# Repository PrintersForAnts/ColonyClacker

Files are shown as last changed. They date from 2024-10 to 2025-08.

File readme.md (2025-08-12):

# 🐜 Colony Clacker

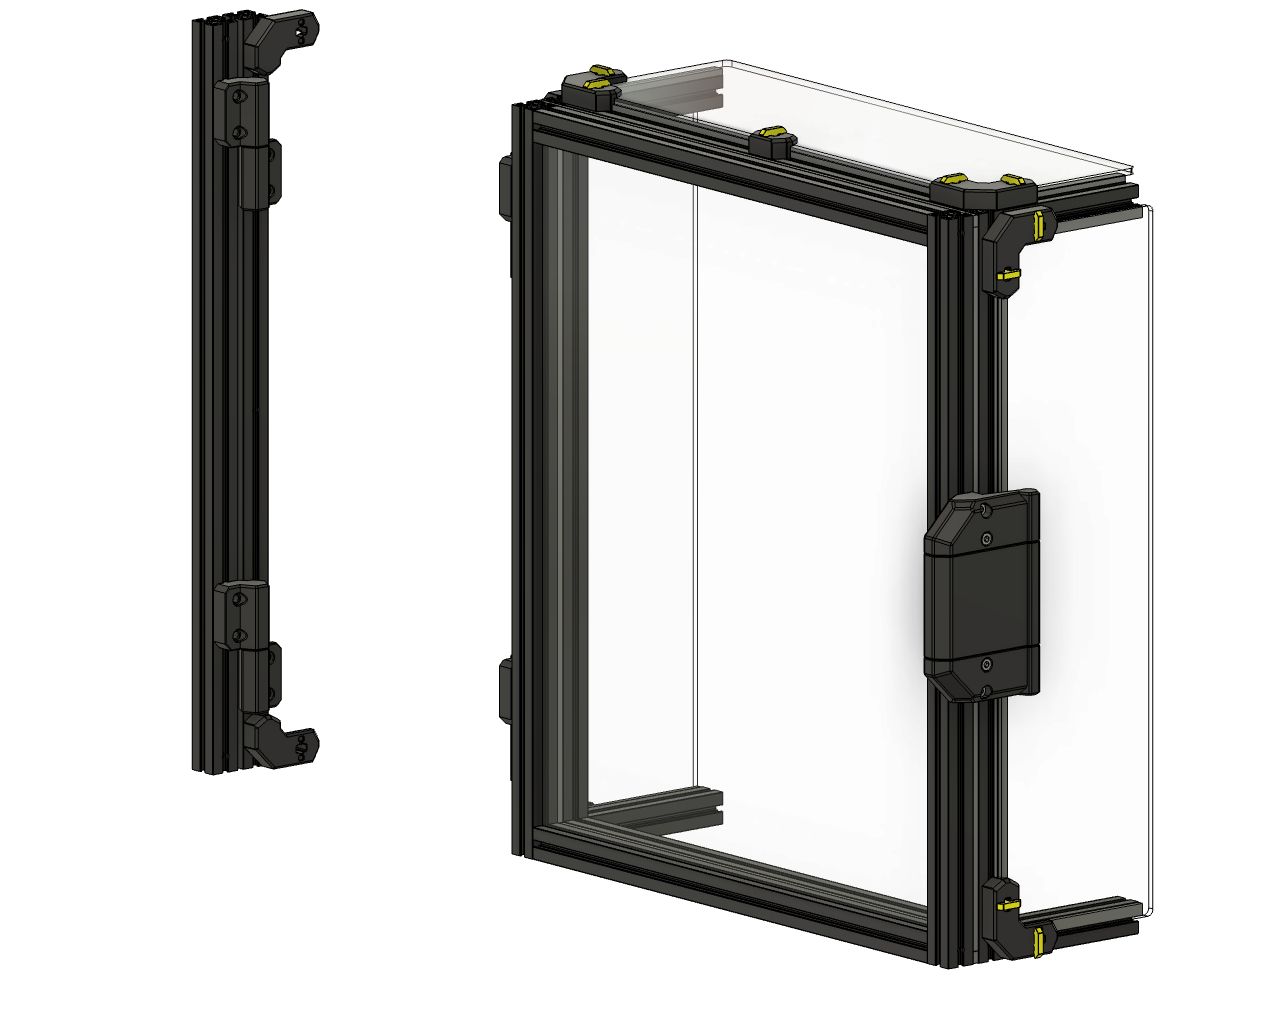
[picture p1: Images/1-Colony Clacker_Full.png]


*A satisfyingly clicky door upgrade for your Printers for Ants colony—because even tiny printers deserve a proper "clack"!*

<p align="center">
  <a aria-label="Stars" href="https://github.com/PrintersForAnts/ColonyClacker/stargazers">
    </a> &nbsp;

  <a aria-label="Forks" href="https://github.com/PrintersForAnts/ColonyClacker/network/members">
    </a> &nbsp;

  <a aria-label="License" href="https://github.com/PrintersForAnts/ColonyClacker/blob/main/LICENSE">
    </a> &nbsp;

  <a aria-label="Commits" href="https://github.com/PrintersForAnts/ColonyClacker/commits/main">
    </a> &nbsp;

  <a aria-label="Discord" href="https://discord.gg/doomcube">
    </a>

<a aria-label="Last Commit" href="https://github.com/PrintersForAnts/ColonyClacker/commits/main">
  
</a>
</p>

## Table of Contents

- [🚪 What is Colony Clacker?](#-what-is-colony-clacker)
- [📦 Bill of Materials](#-bill-of-materials)
- [📐 Door Parts](#-door-parts)
- [🌍 Vendors](#-vendors)
- [🖨️ Print Recommendations](#️-print-recommendations)
- [🔧 Latch & Bottom Hinge Variants](#-latch--bottom-hinge-variants)
- [🎨 Handle_C Logo Variants](#-handle_c-logo-variants)
- [🛠️ Assembly Instructions](#️-assembly-instructions)
- [🎨 Optional Skirts](#-optional-skirts)
- [💬 Feedback & Discussion](#-feedback--discussion)
- [🐞 Raising Issues](#-raising-issues)
- [📜 Version History](#-version-history)

---

## 🚪 What is Colony Clacker?

Inspired by the popular [Clicky-Clack Fridge Door](https://github.com/tanaes/whopping_Voron_mods/tree/main/clickyclacky_door) mod by tanaes, **Colony Clacker** is specially designed for Printers for Ants (PFA), and other 1515 based printers.

Completely remodeled from scratch (not just scaled), it boasts enhanced stealthy aesthetics, improved tolerances, and optimized STLs for top quality printing using standard Voron settings.

[🎥 Watch the satisfying Clack in action!](https://youtube.com/shorts/yi75DsFQ0eI?si=P8Z4A60wTr4WiRiI)

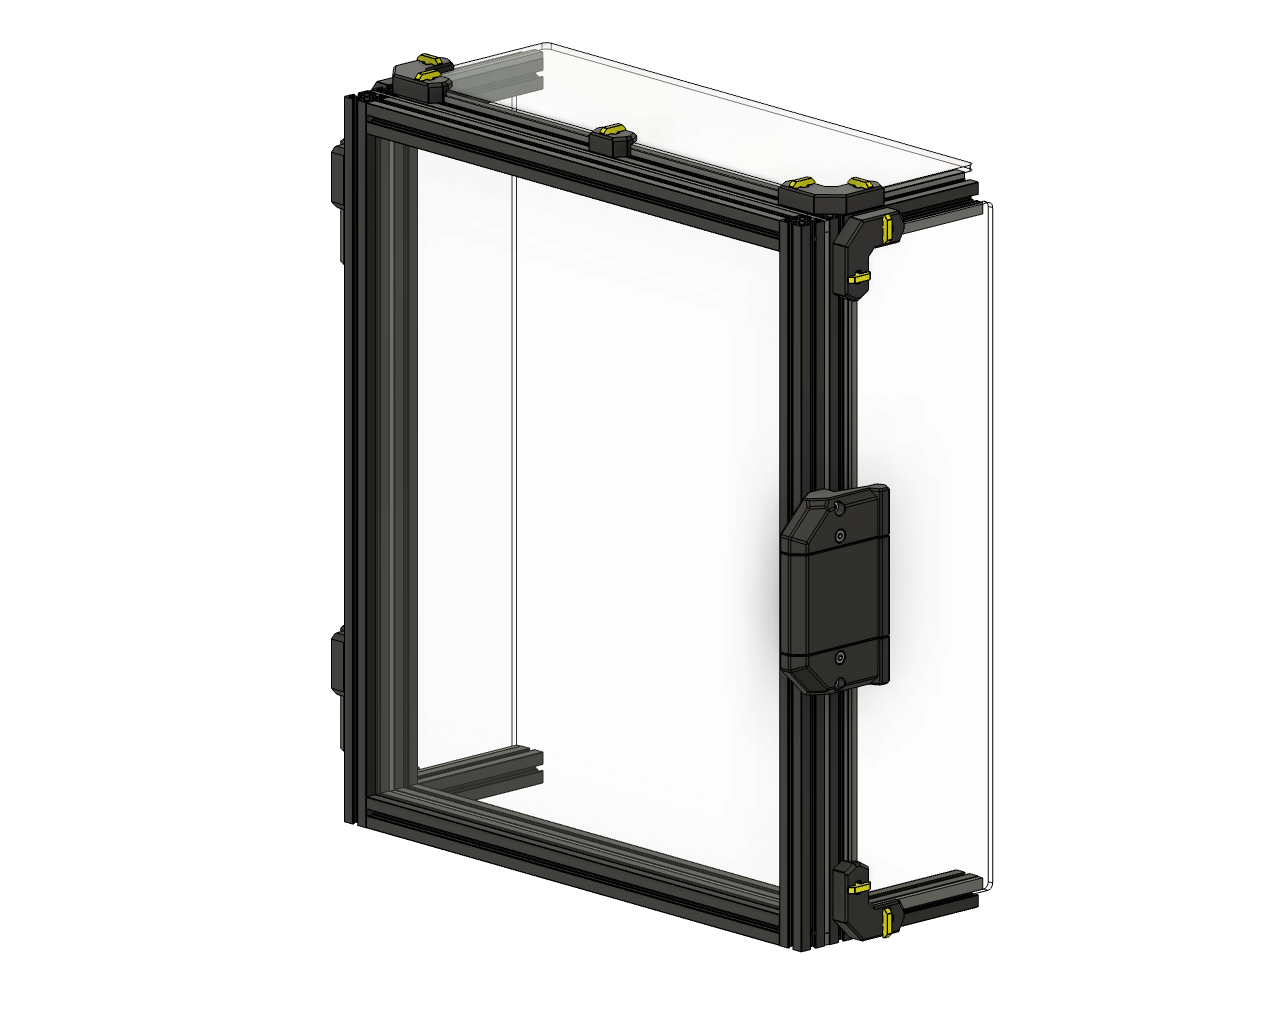
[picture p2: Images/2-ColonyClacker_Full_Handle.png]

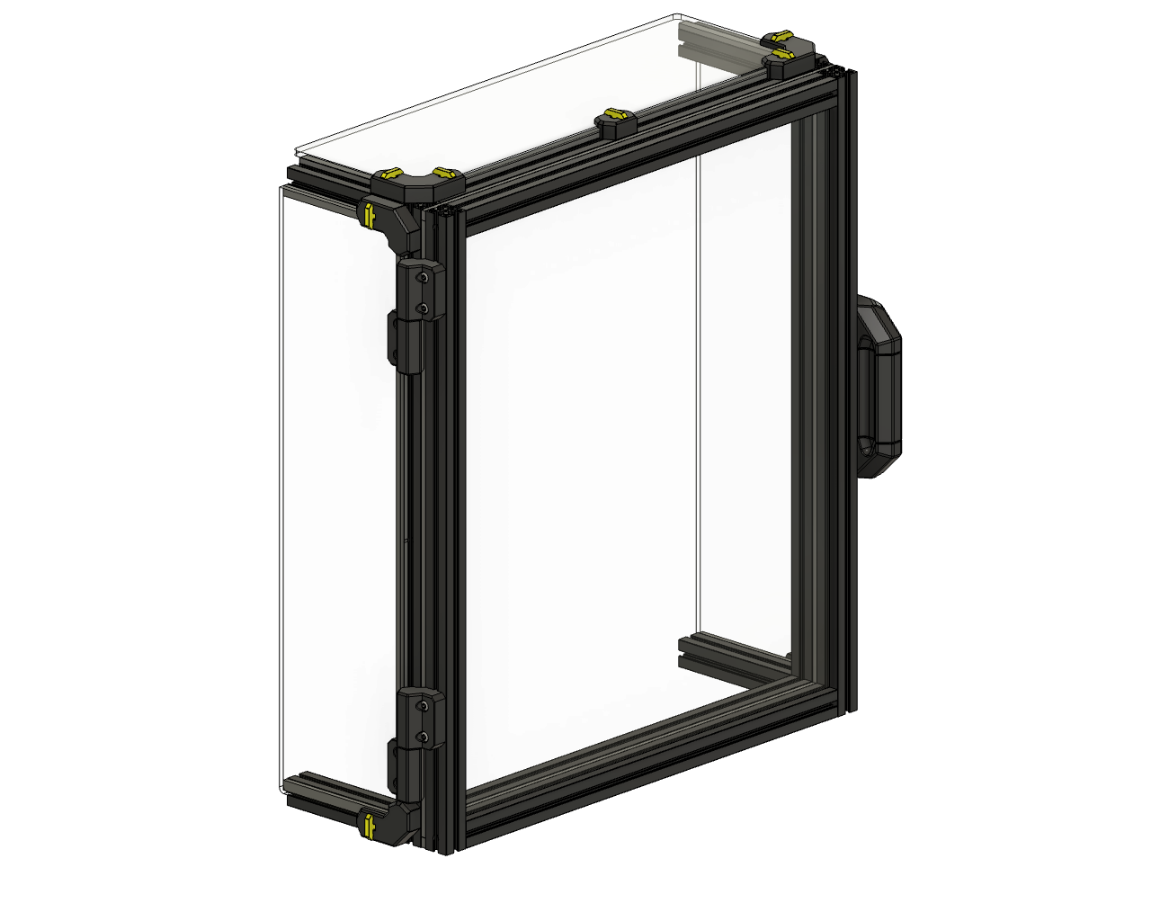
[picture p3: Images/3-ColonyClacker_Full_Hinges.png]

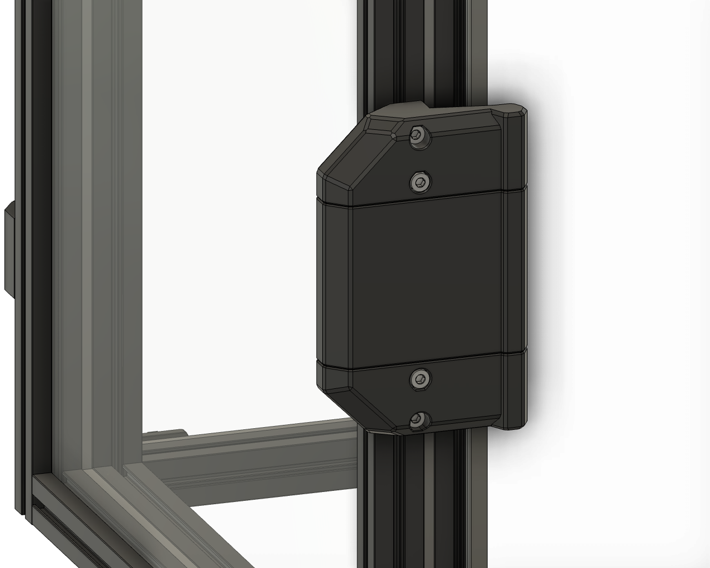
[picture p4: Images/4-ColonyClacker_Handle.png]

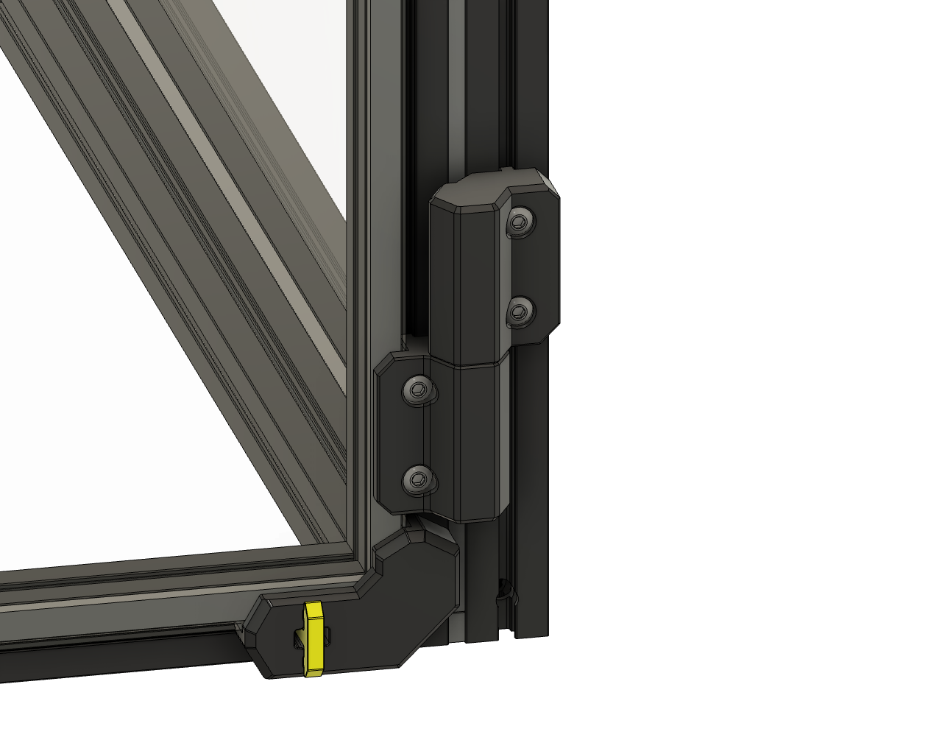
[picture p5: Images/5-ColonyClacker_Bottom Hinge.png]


---

## 📦 Bill of Materials
*If you intend to use the optional extended skirts, additional hardware for these is listed further down the page, in the corresponding skirt sections.*

---

### 🛠️ Hardware
| Qty | Item  | Notes  | Purchase Links  |
| :---: | :---- | :----- | :--- |
| 4 | M3x8 BHCS | For blind joints | [Aliexpress](https://s.click.aliexpress.com/e/_Exdxtsp) |
| 10 | M3x12 BHCS |  | [Aliexpress](https://s.click.aliexpress.com/e/_Exdxtsp) |
| 4 | M3x16 SHCS |  | [Aliexpress](https://s.click.aliexpress.com/e/_EGPNidr) |
| 2 | M3x20 SHCS |  | [Aliexpress](https://s.click.aliexpress.com/e/_EGPNidr) |
| 14 | M3 Hex Nut |  | [Aliexpress](https://s.click.aliexpress.com/e/_EwEY3Rf), [Amazon](https://amzn.to/3NtQHXi) |
| 4 | M5 x 7mm x 8mm Split Bushing |  | [Aliexpress](https://s.click.aliexpress.com/e/_EvcAzIV), [Amazon](https://amzn.to/3Yrq8rT) |
| 4 | 5mm x 40mm Dowel Pin |  | [Aliexpress](https://s.click.aliexpress.com/e/_Ex91QWD), [Amazon](https://amzn.to/40eAuNr) |
| 8 | 6mm x 3mm N52 Magnet |  | [Aliexpress](https://s.click.aliexpress.com/e/_EIDUzuD), [Amazon](https://amzn.to/3YqHEga) |
| 1.3M  | 3mm Foam Tape | 2.5M required for double seals | [Aliexpress/Amazon](https://s.click.aliexpress.com/e/_EzqH685) |
| 4 | Micron R1 Twist Lock Key | Printed component | [STL File](https://github.com/PrintersForAnts/Micron/blob/main/STLs/Panels/%5Ba%5D_twist_lock_key_x50.stl) |

> ### *Note* - LDO Rev1 kits will be shipped with M3x12 BHCS for the blind joints, these may need swapping out for M3x8 BHCS if the threads seem tight part way through.

## 📐 Door Parts

### Micron+
| Qty | Item |
| :---: | :---- |
| 2 | 350mm 1515 Aluminium Extrusion |
| 2 | 280mm 1515 Aluminium Extrusion |
| 1 | 3mm Acrylic or PC Panel - 330mm x 290mm |

### StealthFork 180
| Qty | Item |
| :---: | :---- |
| 2 | 400mm 1515 Aluminium Extrusion |
| 2 | 290mm 1515 Aluminium Extrusion |
| 1 | 3mm Acrylic or PC Panel - 380mm x 300mm |

### StealthFork 160
| Qty | Item |
| :---: | :---- |
| 2 | 400mm 1515 Aluminium Extrusion |
| 2 | 270mm 1515 Aluminium Extrusion |
| 1 | 3mm Acrylic or PC Panel - 380mm x 280mm |

### Voron V0 (80mm Top Hat)
| Qty | Item |
| :---: | :---- |
| 2 | 330mm 1515 Aluminium Extrusion |
| 2 | 200mm 1515 Aluminium Extrusion |
| 1 | 3mm Acrylic or PC Panel - 310mm x 210mm |

### Voron V0 (100mm Top Hat)
| Qty | Item |
| :---: | :---- |
| 2 | 350mm 1515 Aluminium Extrusion |
| 2 | 200mm 1515 Aluminium Extrusion |
| 1 | 3mm Acrylic or PC Panel - 330mm x 210mm |

---

## 🌍 Vendors

| Country | Vendor | Notes |
|:--:|:--|:--|
| 🇬🇧 | [OneTwo3D](https://www.onetwo3d.co.uk/product/ldo-colony-clacker-kit-for-micron/?wpam_id=11) | LDO Kit (Affiliate Link) |
| 🇬🇧 | [ViperWorx](https://www.viperworx.uk/product/colony-clacker-door-panel-for-micron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) | Panel Only |
| 🇪🇺 | [MyRigs](https://myrigs3d.com/collections/printer-for-ants/products/ldo-colony-clacker-kit-for-micron) | LDO Kit |
| 🇺🇸 | [DLLPDF](https://www.dllpdf.com/colony-clacker) | Extrusions, hardware, panels |
| 🇺🇸 | [Fabreeko](https://www.fabreeko.com/products/ldo-micron-160-180-colony-clacker-door-kit-1?_pos=1&_psq=colony&_ss=e&_v=1.0) | LDO Kit, + Optional Panel |
| 🇺🇸  | [West3D](https://west3d.com/products/colony-clacker-door-kit-for-micron-with-or-without-panel-fridge-door-clicky-clack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) | LDO Kit |
| 🇭🇺 | [Zen3D](https://shop.zen3d.hu/colony-clacker-door-black) | LDO Kit (Hungary) |

---

## 🖨️ Print Recommendations

**All STLs are pre-oriented for printing.**

- **Material:** ABS or ASA
- **Layer height:** 0.20 mm (including first layer)
- **Wall count:** 4
- **Extrusion width:** 0.40 mm (forced)
- **Top/bottom solid layers:** 5
- **Infill:** 40% (Grid, Gyroid, Honeycomb, Triangle, or Cubic)
- **Supports:** Not required

---

### 🔧 Latch & Bottom Hinge Variants

Available in multiple offsets to suit different panel/foam thicknesses. The required frame‑to‑door distance is embossed on the back of each STL (e.g., **6** = **6 mm**).

Thicknesses range from **2.8 mm** to **6.0 mm** in **0.2 mm** increments.

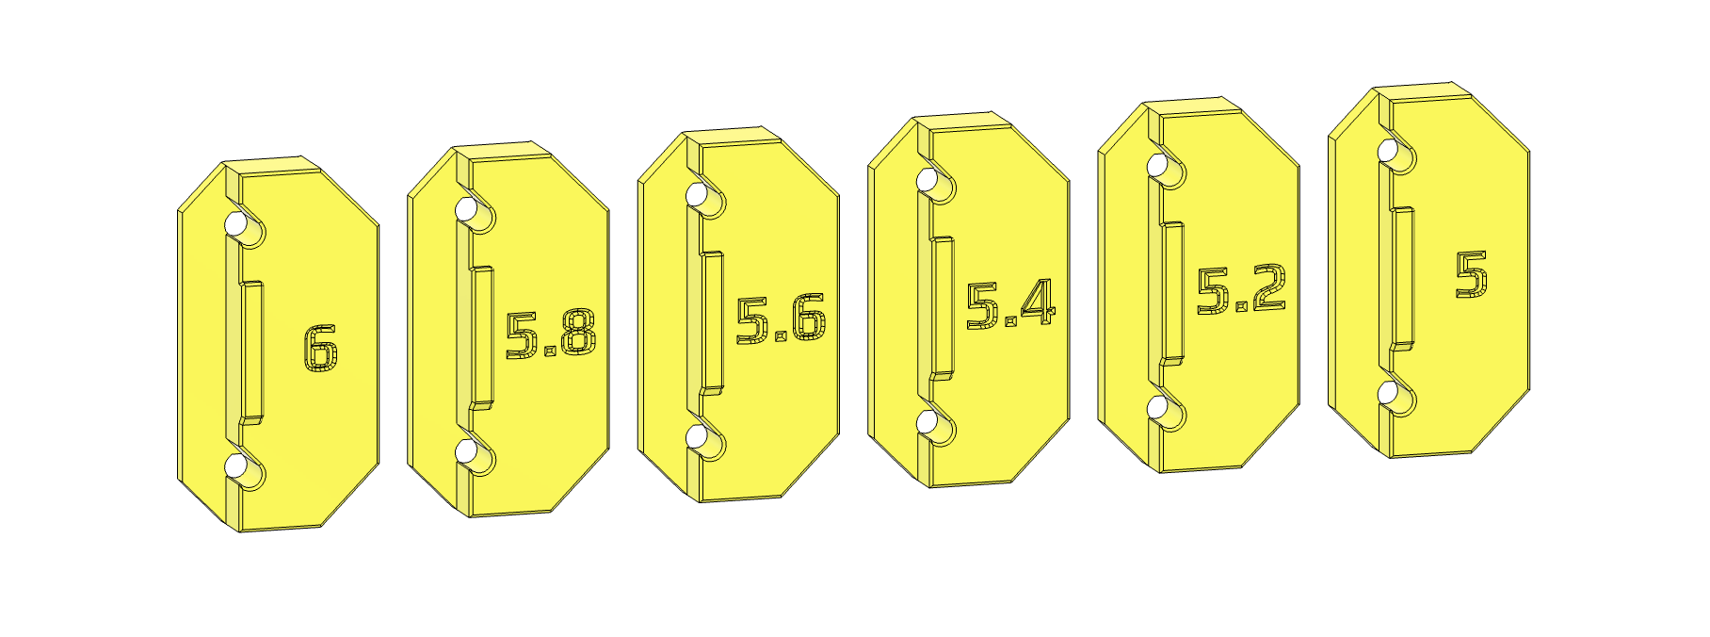
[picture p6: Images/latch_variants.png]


*Bottom hinge variants with varying pin offsets for different panel/foam thicknesses.*

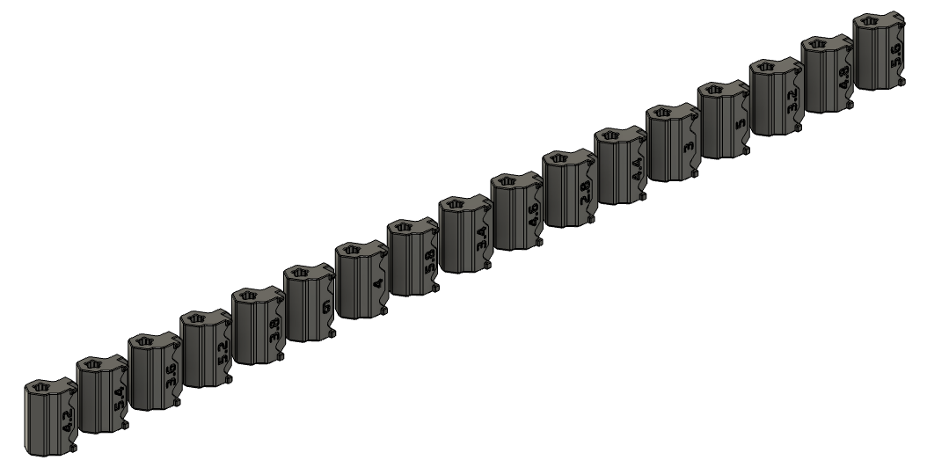
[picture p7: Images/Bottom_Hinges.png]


---

### 🎨 Handle_C Logo Variants

Handle_C versions are available with logos from various brands and printers, allowing you to customise your build.

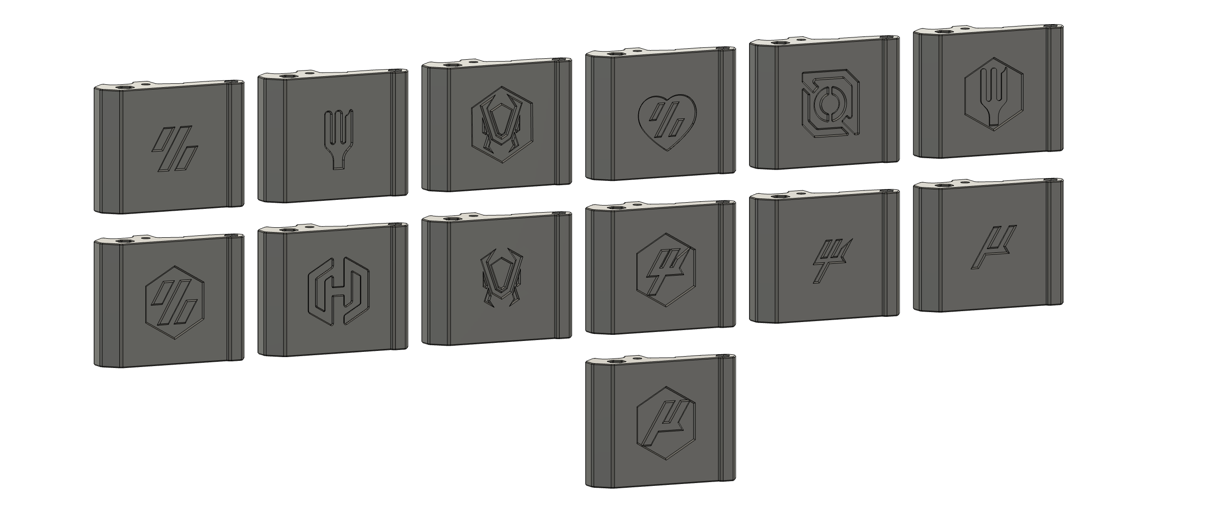
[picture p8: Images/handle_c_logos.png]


---

## 🛠️ Assembly Instructions
Assembly is intuitive. Use the provided images for visual guidance if you encounter difficulties.

To aid with aligning the door when installing it, a sacrificial layer has been modelled into the lower hinge.  
Apply a little extra force when inserting **one** of the pins. This will make that pin shorter, allowing you to align one hinge at a time. 

**Important:**
- Secure magnets with superglue into the latch and corresponding handle piece
- Hardware locations can be seen in the assembly images below.
- On initial build, you may experience less clacking, this is usually due to the foam needing to settle, or the 2x screws in the latch being too tight.

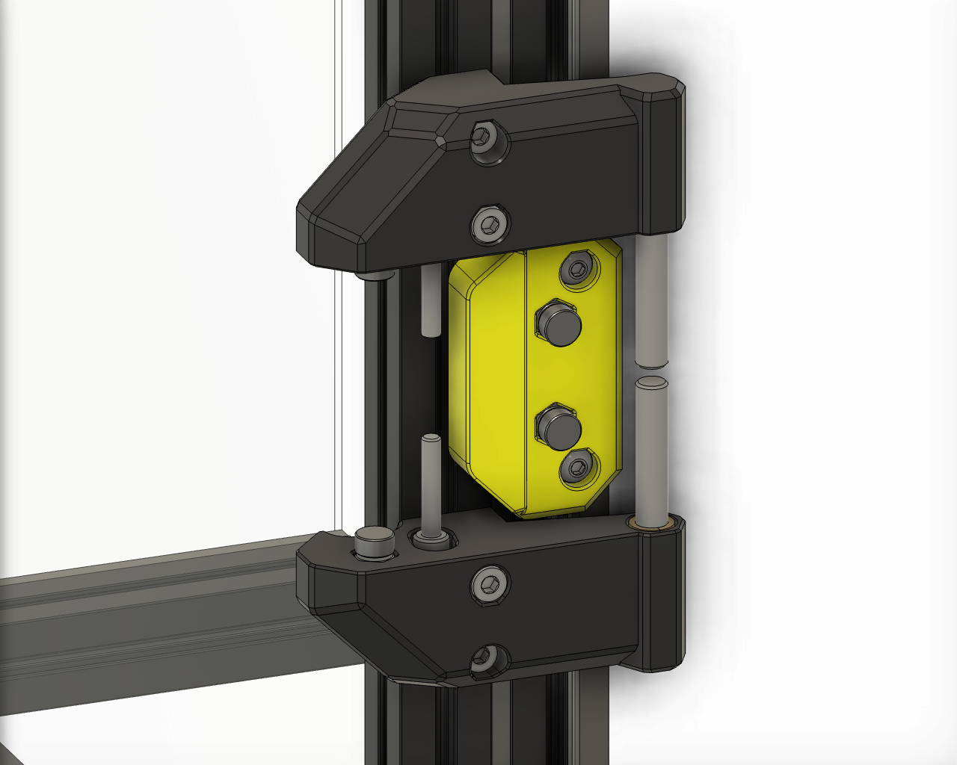
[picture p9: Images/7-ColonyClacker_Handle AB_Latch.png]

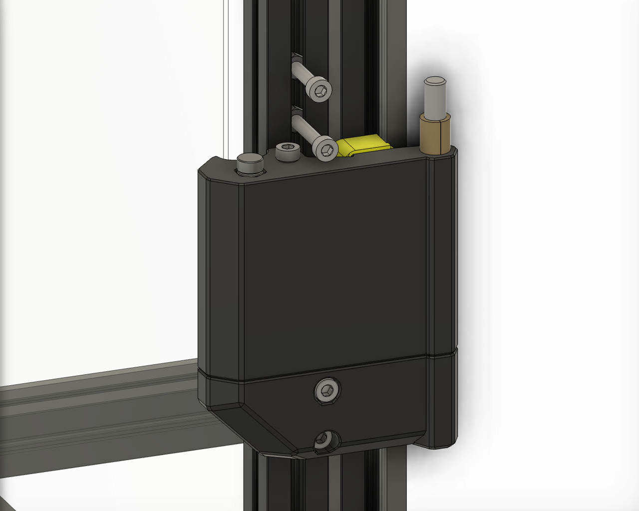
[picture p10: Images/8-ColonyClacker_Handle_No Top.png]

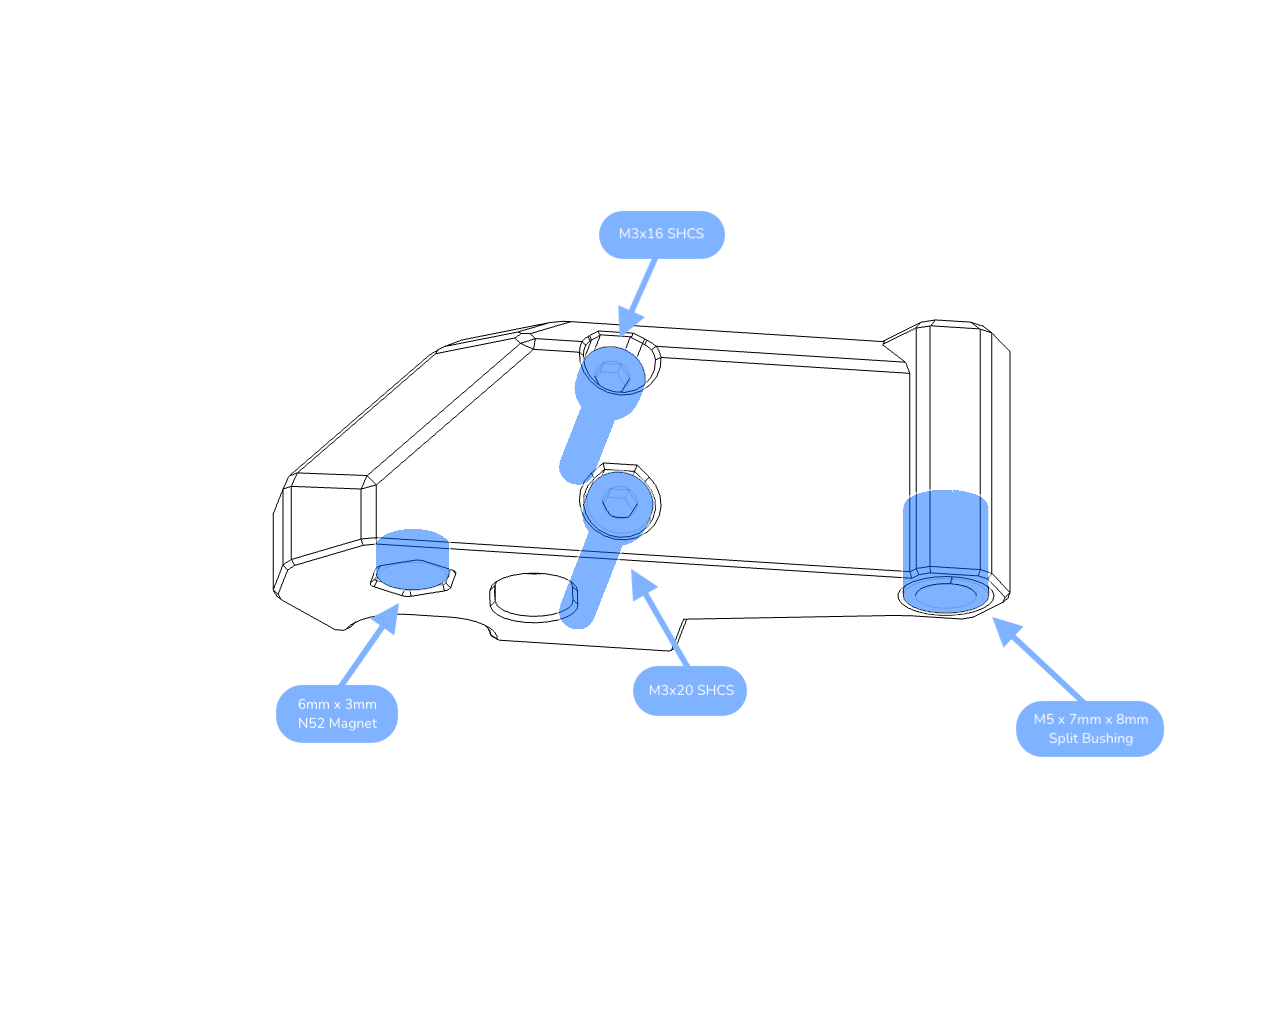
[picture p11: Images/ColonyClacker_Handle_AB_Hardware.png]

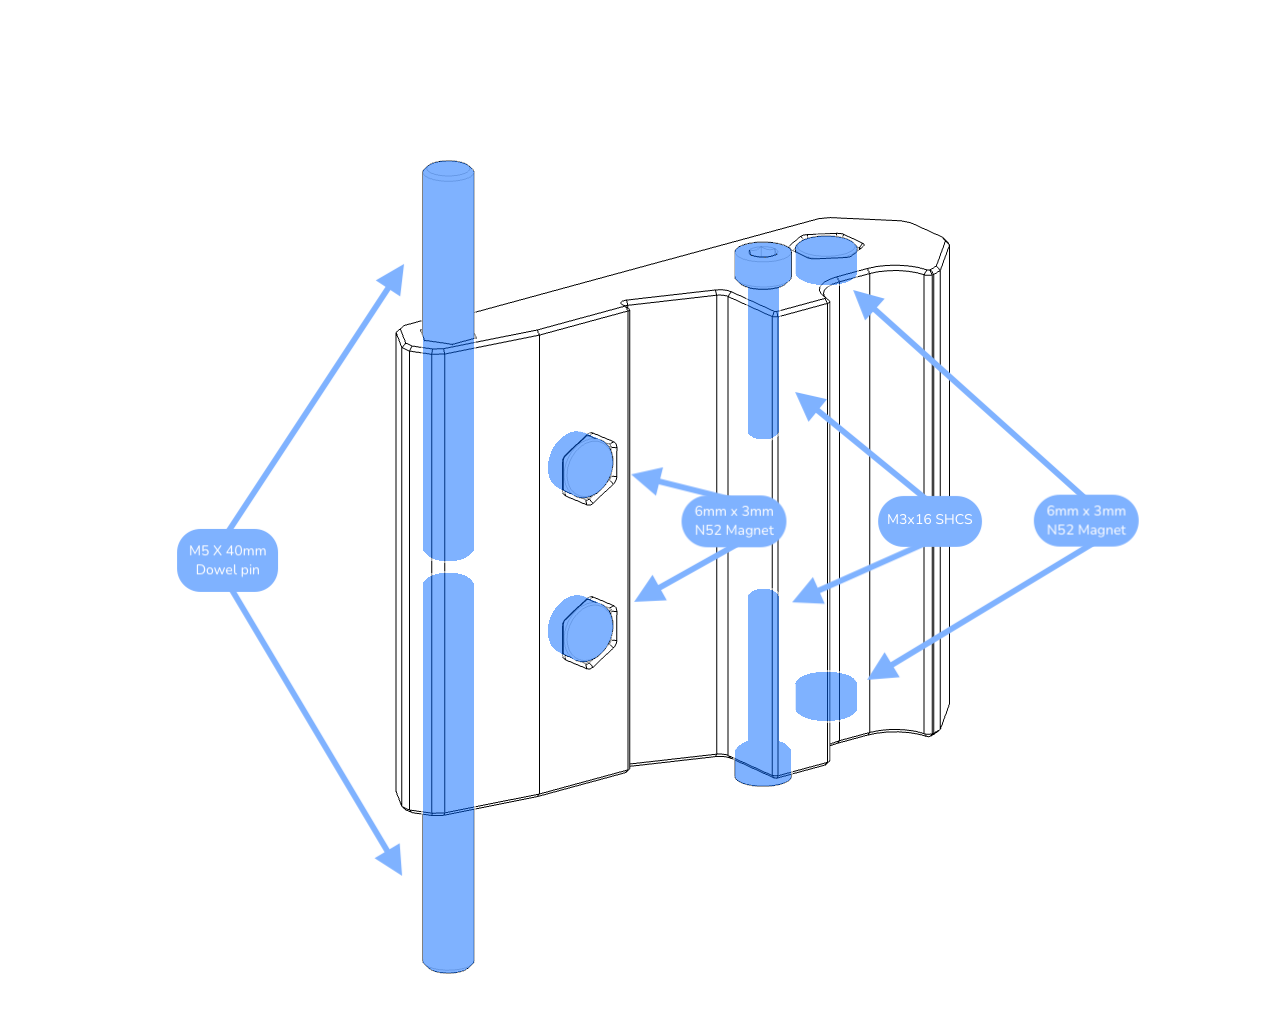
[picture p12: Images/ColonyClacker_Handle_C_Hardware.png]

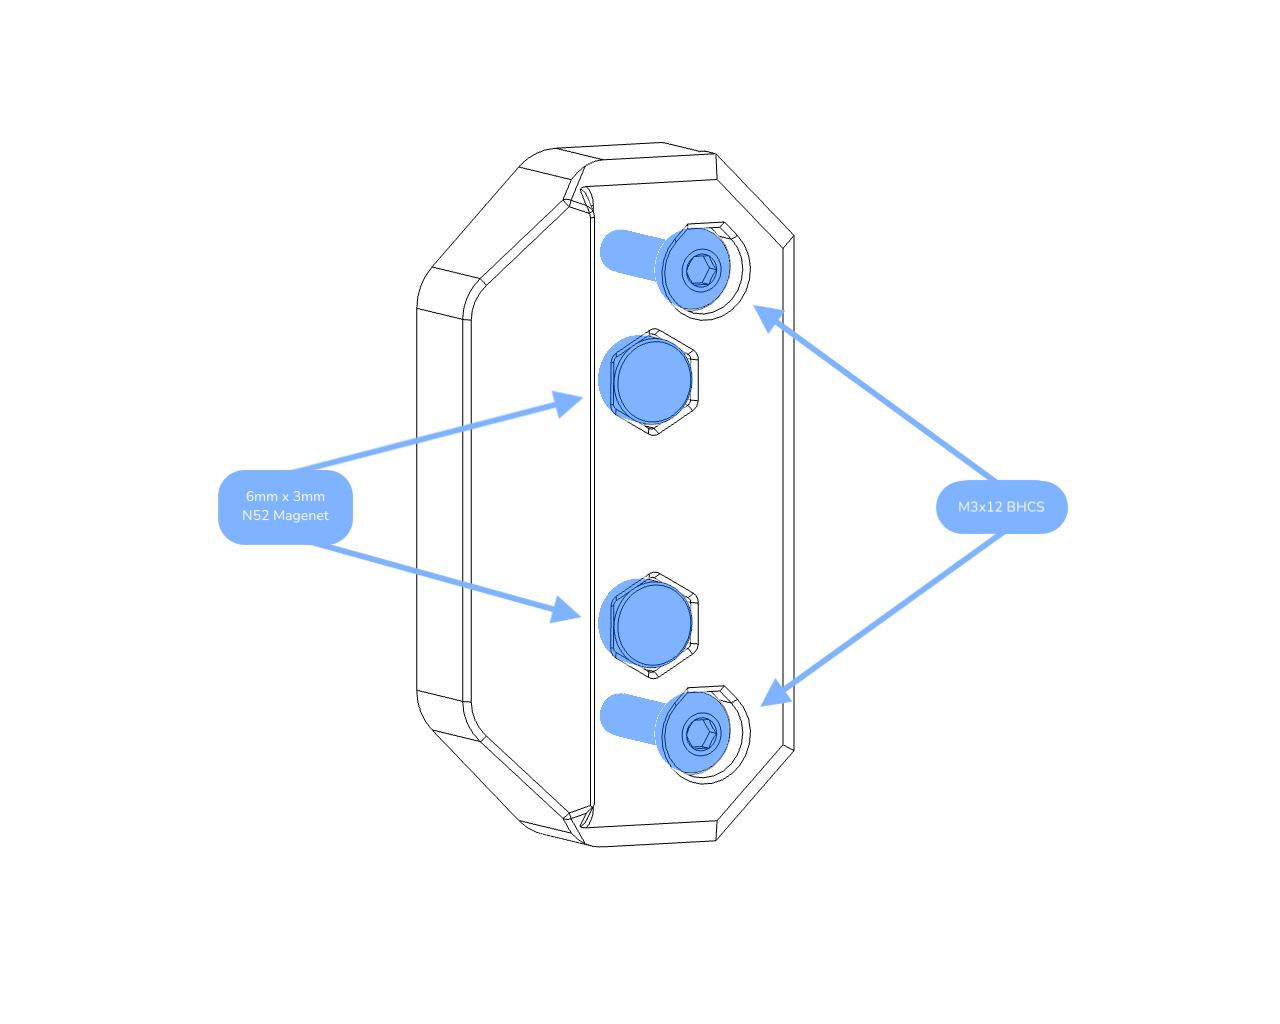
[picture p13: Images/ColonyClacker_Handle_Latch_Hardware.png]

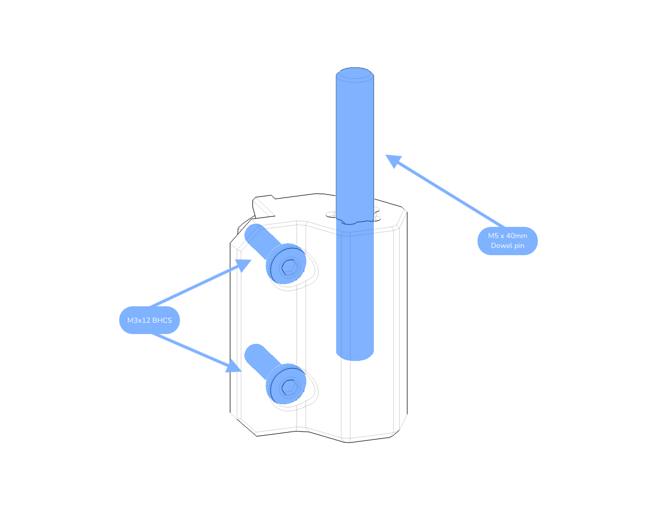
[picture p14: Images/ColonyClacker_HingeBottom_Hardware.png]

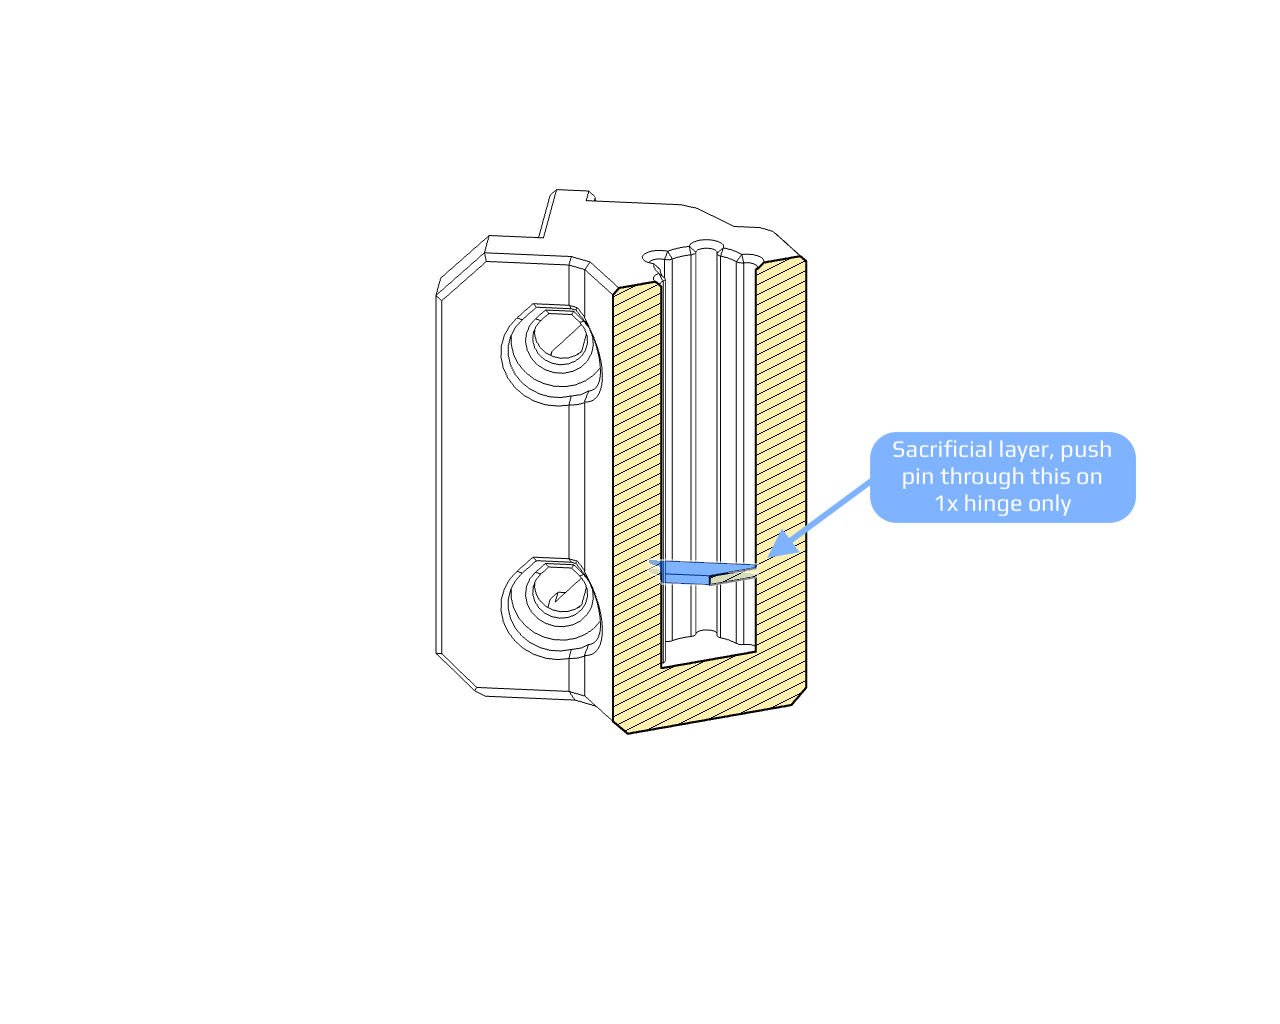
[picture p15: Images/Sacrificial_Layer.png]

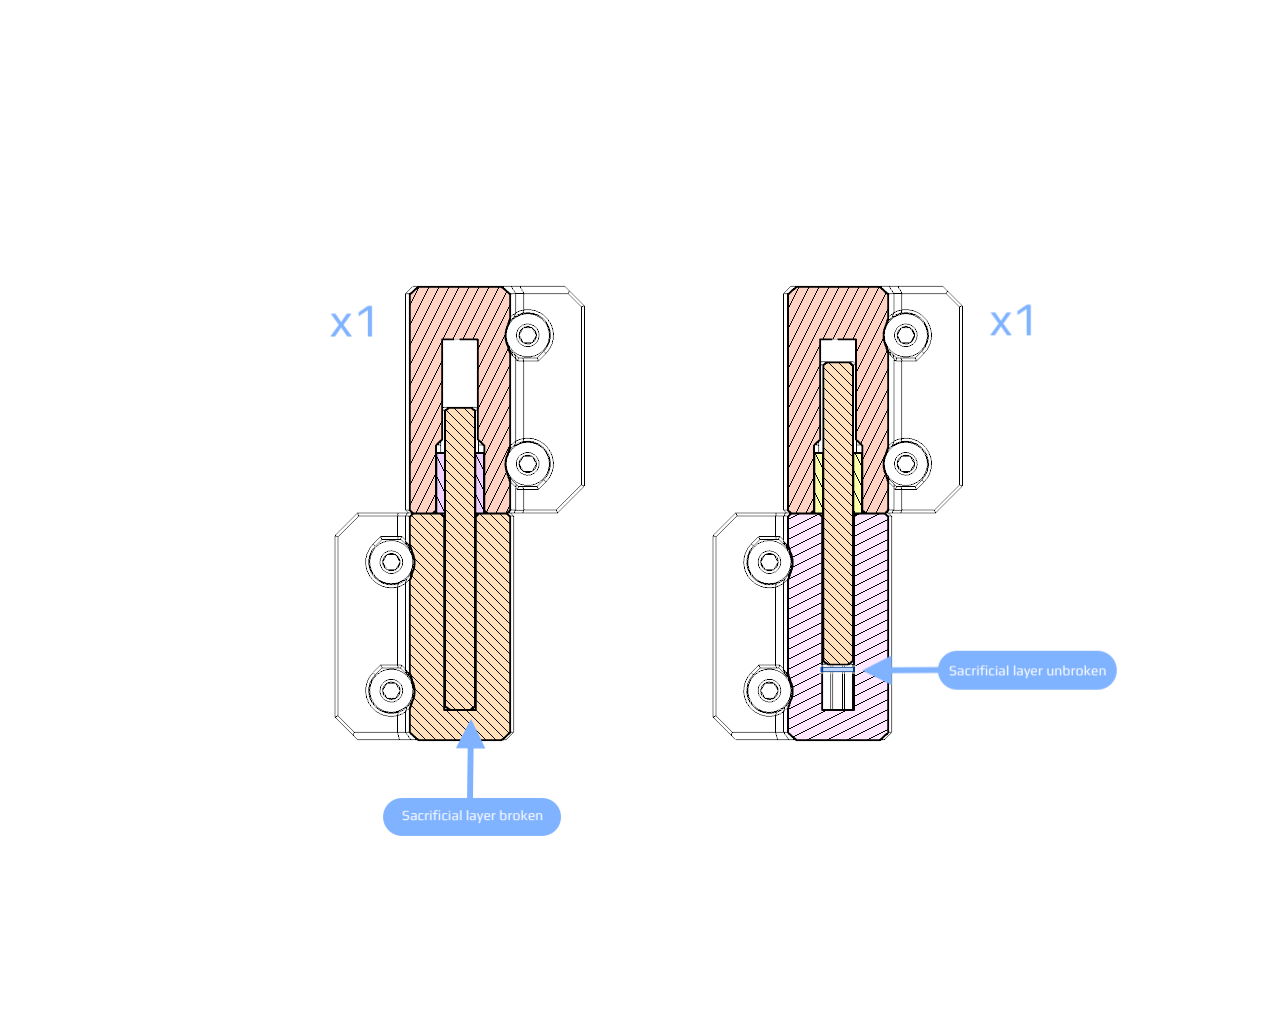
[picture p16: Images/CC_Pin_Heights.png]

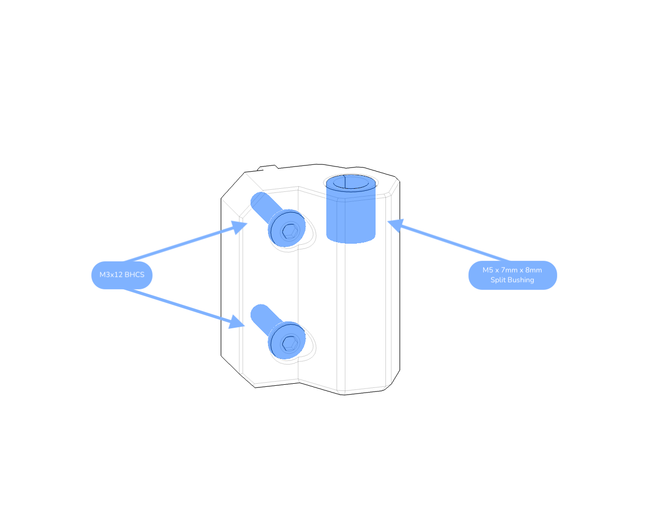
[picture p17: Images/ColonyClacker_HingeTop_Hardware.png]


---

## 🎨 Optional Skirts 
There are currently some extended skirts for the following PFA Printers.
They improve overall aesthetics and screen access.
(Others will be added as they are created)

**Micron+ (G2Z)**  

| Qty | Additional Hardware |
|:-----:|:---|
| 2 | M3x5x4 Heatset Insert |
| 2 | M3x8 BHCS |

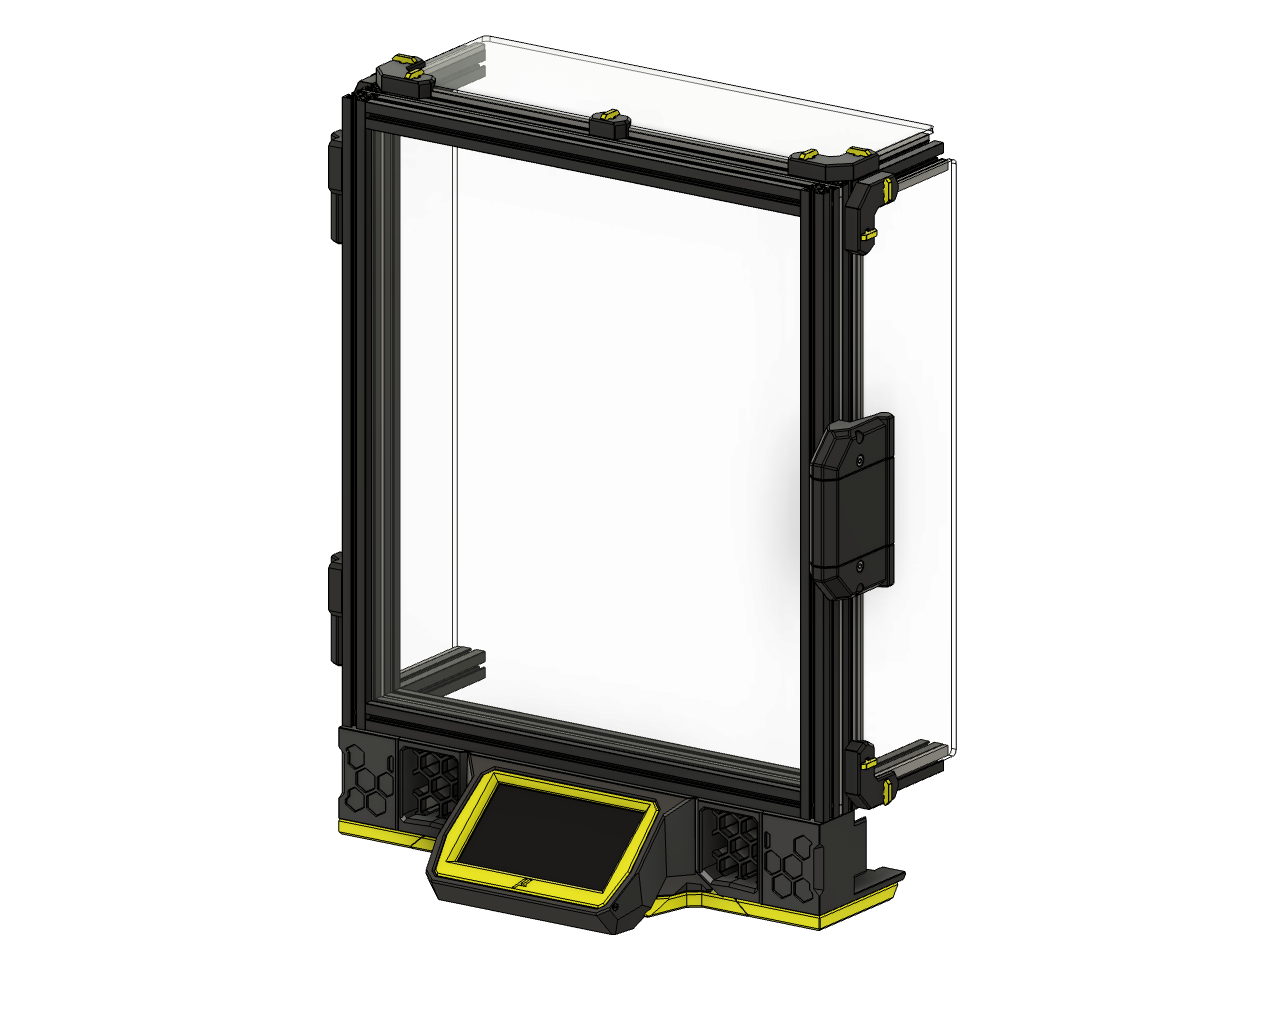
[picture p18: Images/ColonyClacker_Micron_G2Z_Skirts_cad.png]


**Micron+ (Stock Z)**

| Qty | Additional Hardware |
|:-----:|:---|
| 4 | M3x5x4 Heatset Insert |
| 4 | M3x8 BHCS |
| 8 | M2x10 STS |

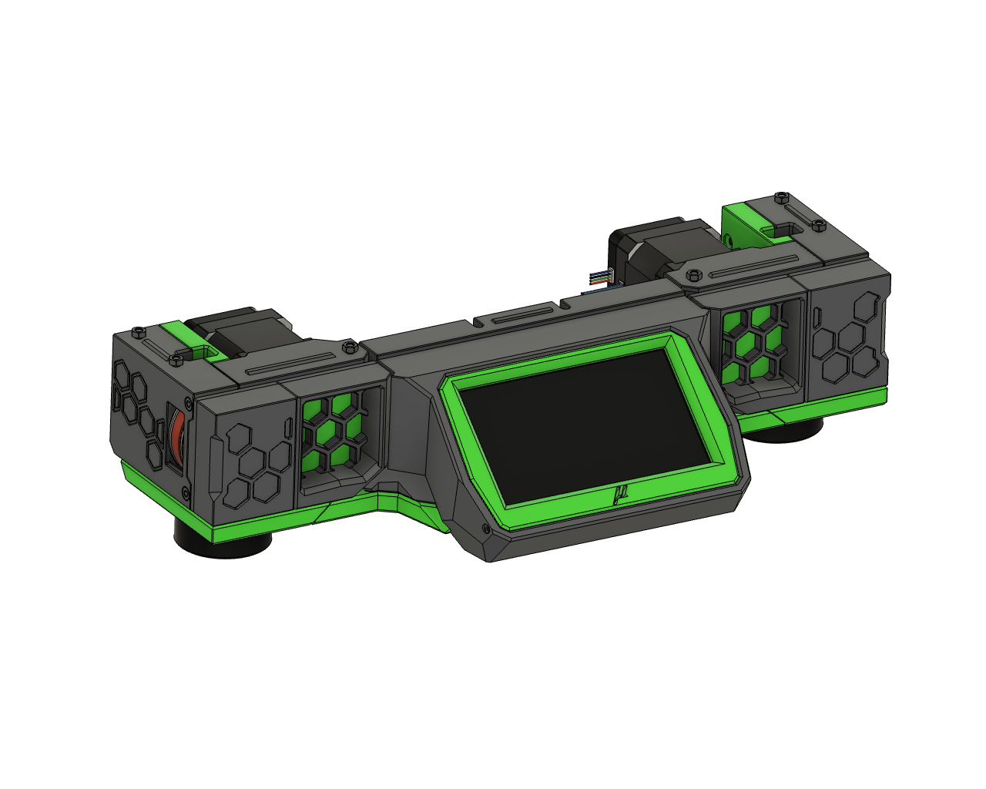
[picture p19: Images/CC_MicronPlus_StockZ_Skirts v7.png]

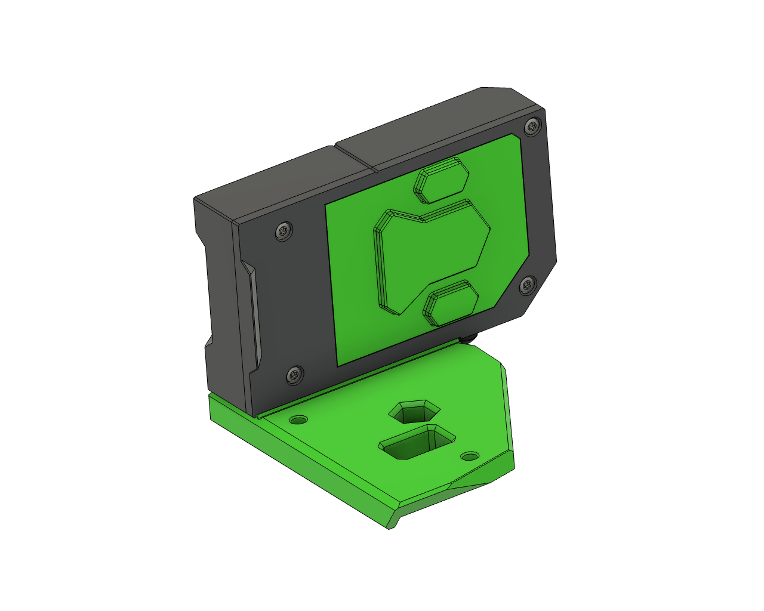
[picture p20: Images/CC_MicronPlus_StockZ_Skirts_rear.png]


**StealthFork**

| Qty | Additional Hardware |
|:-----:|:---|
| 4 | M3x5x4 Heatset Insert |
| 4 | M3x8 BHCS |

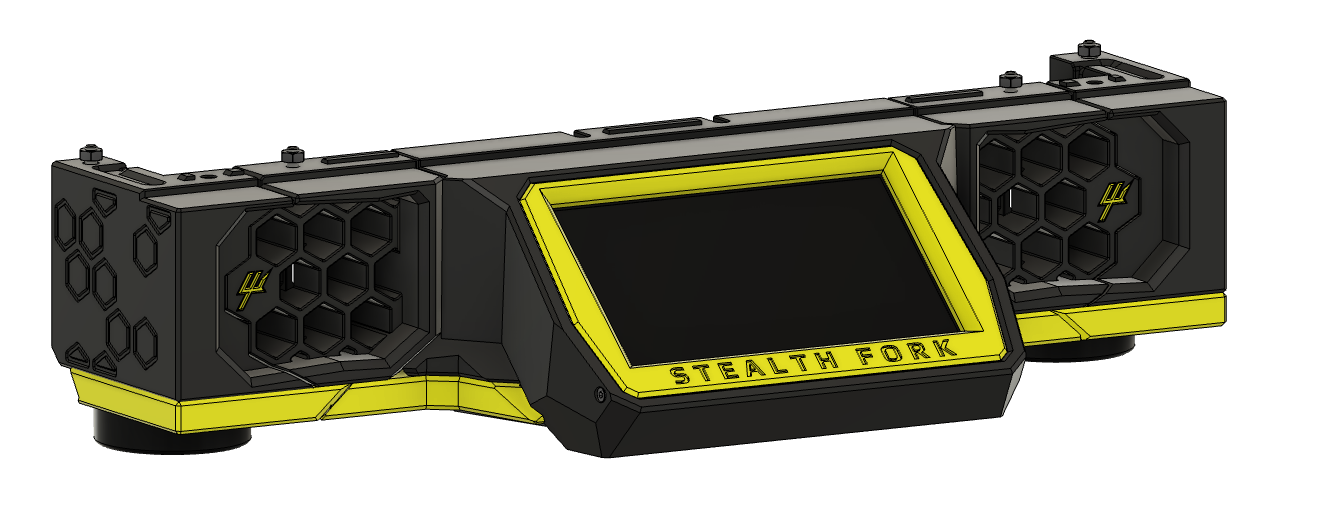
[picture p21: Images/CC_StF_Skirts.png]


---

## 💬 Feedback & Discussion  

If you're building a Colony Clacker, we'd love to hear your thoughts! 

Join the discussion, suggest improvements, or share feedback in the 'KyleGB' channel on the Doomcube Discord.  

---

## 🐞 Raising Issues
If you encounter any issues, please report them via the Issues section on the Git repository. 

Be as detailed as possible, include steps to reproduce, and relevant images or screenshots. 

Your feedback helps improve Colony Clacker for everyone!

---

## 📜 Version History

| Date | Change Details |
|---|---|
| **10-Aug-25**  | Clean up of folders<br>Increased diameter of screw head recess on hinges by 0.1mm and added flat for increased printability<br>Added **Sacrificial Bridge** to `bottom_hinge_frame_mount.stl` to allow one hinge to have a shorter pin for easier door alignment<br>added variants of `bottom_hinge_frame_mount.stl` to allow for different panel/foam thicknesses<br>Added list of vendors to readme.md|
| **09-Aug-25**  | Added new latch, updated for better printability with variants for panel distance.<br>Added Handle_C logo variants.<br>CAD updated with LDO extrusions to match kits. |
| **24-May-25**  | Added StealthFork 160 & 180 Skirts<br>Added TFT35 Display Mount<br>Moved Micron+ Stock Z Skirts CAD to archive |
| **22-Mar-25**  | Fixed missing heatset hole on `skirt_main_body.stl`, relocated screw for better clearance from M2x10 STS (Thanks dajones89) |
| **21-Mar-25**  | Added Micron R1 Stock Z Skirts.<br>Added v1.1 of Micron+ G2Z skirts - 2mm clearance added for door.<br>Moved v1 files to archive folder. |
| **13-Mar-25**  | Clean-up `readme.md` |
| **12-Mar-25**  | Fixed Issue [#1](https://github.com/PrintersForAnts/ColonyClacker/issues/1) |
| **17-Oct-24**  | Added Larger Surface Area latch variants; Corrected hardware details |
| **10-Oct-24**  | Added missing chamfers; Improved STL naming clarity |
| **08-Oct-24**  | Initial Release 🎉 |

---

Enjoy your clicky-clacking Colony Clacker! 🐜✨

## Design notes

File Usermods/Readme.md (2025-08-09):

## 🧪 User Mods

The following community-made mods enhance or customise the **Colony Clacker** experience.

### 📋 Table Structure

To add your mod, please include:
- Your name or handle
- A link to your sub-folder (in `/Usermods`)
- A short description of your mod

like so:
`| Creator | [Mod title](link) | Description |`

---

| Creator | Mod title | Description |
| --- | --- | --- |
|CabbageCorp| [**Mini Monolith Colony Clacker**](https://github.com/PrintersForAnts/ColonyClacker/tree/main/Usermods/CabbageCorp/Mini%20Monolith%20ColonyClacker)| Mini Monolith compatible Colony Clacker hinge & latch |
|GearNut|[**BTT HDMI5 Display Mount**](https://github.com/PrintersForAnts/ColonyClacker/tree/main/Usermods/Gear_Nut/BTTHMDI5)| Display mount & Bezel for BTT HDMI5 display

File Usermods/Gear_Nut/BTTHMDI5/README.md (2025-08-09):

Took the work that @BlindBadger started and modified it for the CC mod from the amazing Jadecky 

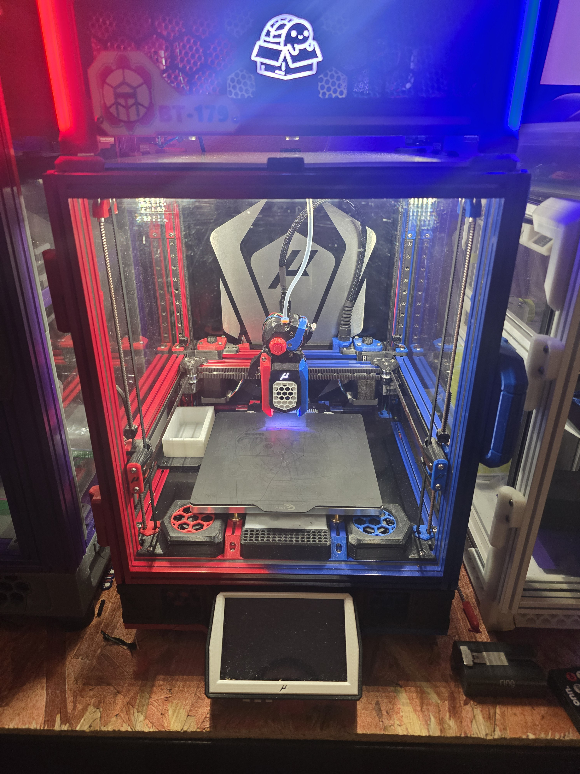
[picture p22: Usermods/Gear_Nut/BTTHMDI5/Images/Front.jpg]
Alt text of the image


I have included the stl for the bezel and screen though I made no changes to those from BlindBadgers work. 

The mount and bezels will fit perfectly with the rest of the CC skirt parts 

It has been printed and tested all parts are oriented for printing and have the nessicary supports in place where needed and should break away clean 

If anything needs fixed feel free to let me know and I will get to it as soon as I can :) 

one thing to note. Depnding on the HDMI cable you use you MIGHT have to trim back the A accent though that will be completely hidden under the mount and even with as far back as I needed to trim mine to use the inclided HDMI cable it does not interfere with any of the mounting holes.

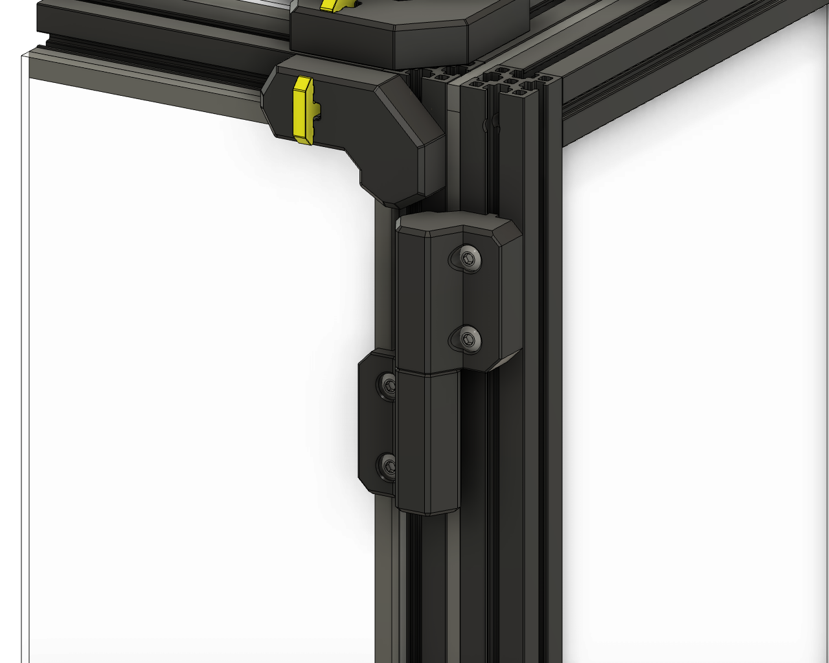
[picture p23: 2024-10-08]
Images/6-ColonyClacker_Top Hige.png

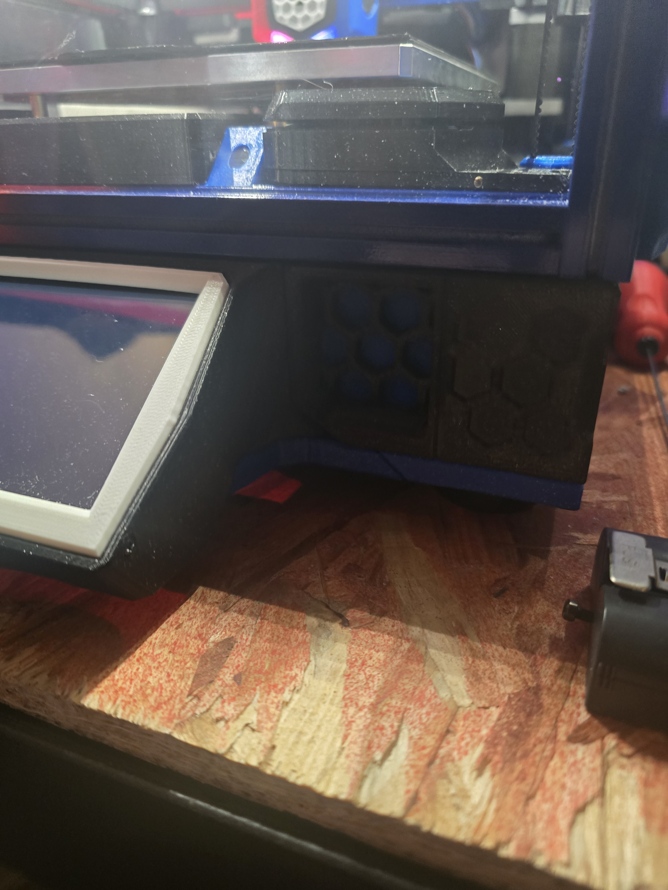
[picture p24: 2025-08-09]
Usermods/Gear_Nut/BTTHMDI5/Images/Right.jpg

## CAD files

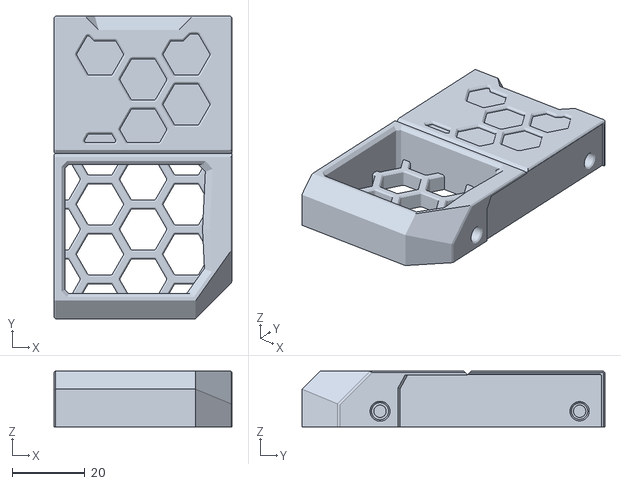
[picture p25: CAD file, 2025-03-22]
STLs/Optional Skirts/Micron+/Stock Z/CC_Micron_StockZ_Skirt_Main_Body_B_x1.stl
49.0 x 83.3 x 15.4

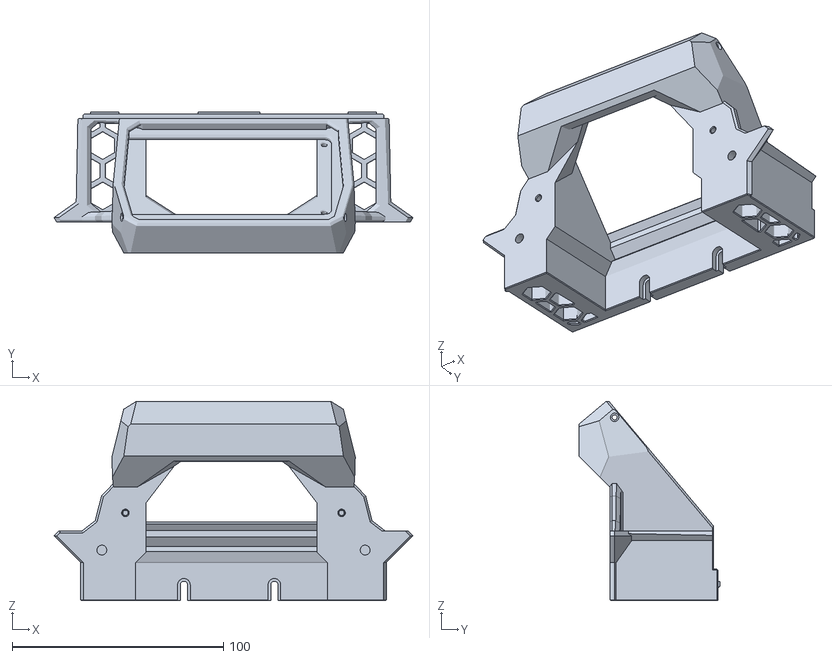
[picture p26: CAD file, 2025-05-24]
STLs/Optional Skirts/Micron+_StealthFork_Common/TFT35/CC_TFT35_Main_housing_x1.stl
169.9 x 66.6 x 94.4

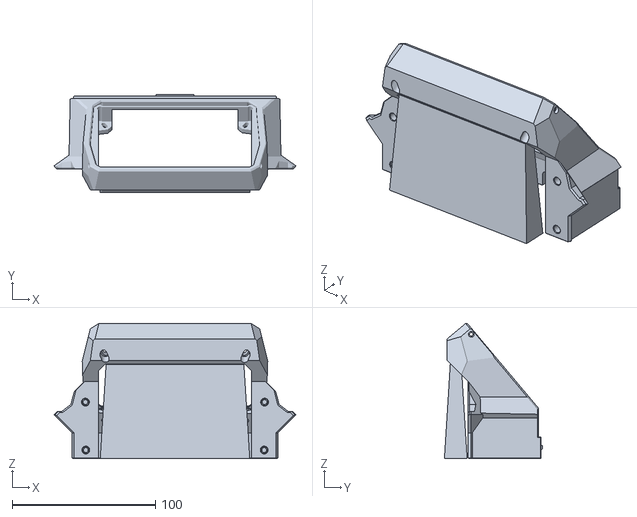
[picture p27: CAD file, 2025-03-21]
STLs/Optional Skirts/Micron+_StealthFork_Common/Waveshare_BTT_43/CC_Waveshare_BTT_43_Main_housing.stl
169.0 x 68.6 x 94.4

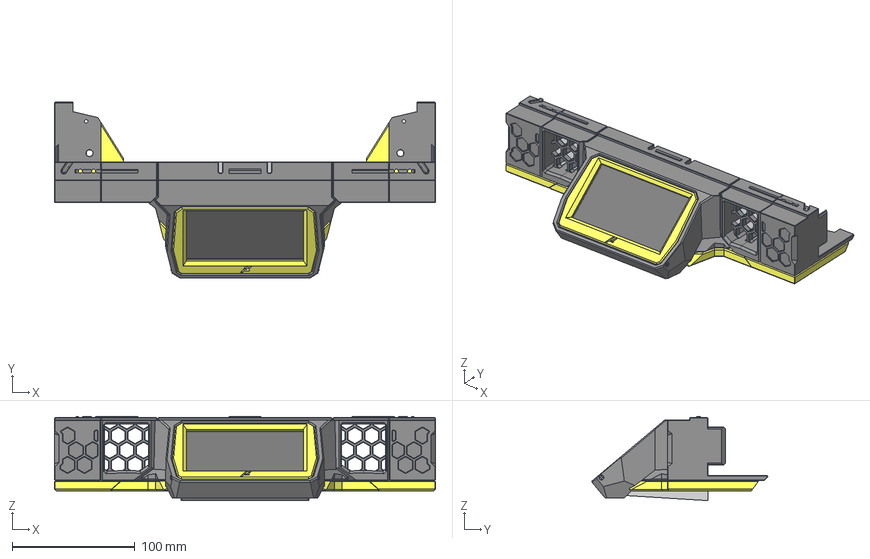
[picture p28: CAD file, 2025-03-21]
CAD/Optional Skirts/CC_MicronPlus_G2Z_Skirts v1.1.step
310.0 x 143.0 x 68.6 mm
Waveshare43
Waveshare_Accent_A
Waveshare_Accent_B
Bezel
Main_housing
M2x10 STS_1 x 2
Foot_Mount_A
G2_Z_Skirt_Corner_A
G2Z_Front_Skirt_A
Foot_Mount_A_1
G2_Z_Skirt_Corner_A_1
G2Z_Front_Skirt_A_1

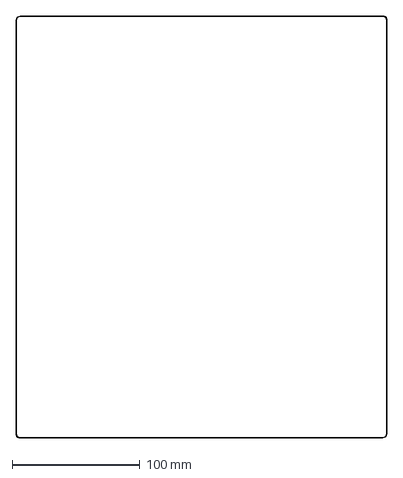
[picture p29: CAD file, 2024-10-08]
DXFs/Colony_Clacker_Micron_Door_Panel.dxf
290.0 x 330.0 mm

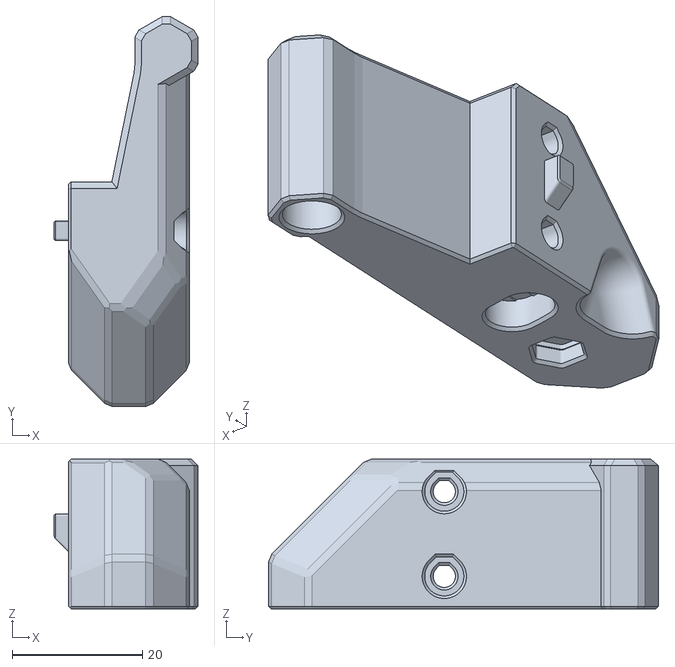
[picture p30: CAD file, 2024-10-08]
STLs/Handle/Handle_A_x1.stl
22.1 x 59.9 x 23.0

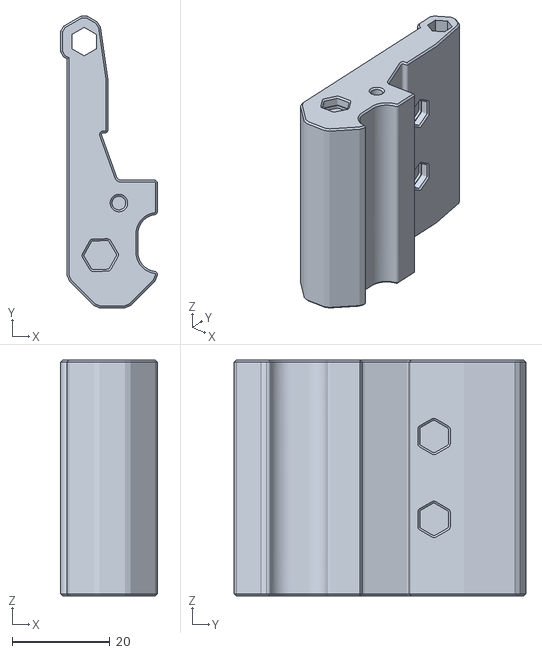
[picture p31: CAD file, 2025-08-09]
STLs/Handle/Handle_C_Logos/Handle_on_left/Handle_C_VoronHeart_L_x1.stl
19.9 x 59.9 x 48.4

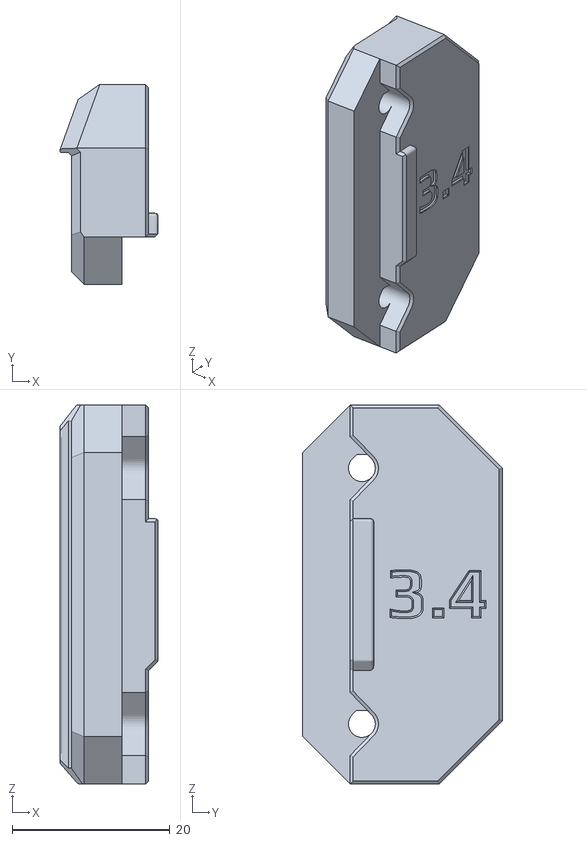
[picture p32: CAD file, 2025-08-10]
STLs/Handle/Latch/Latch_3.4mm_x1.stl
12.5 x 25.3 x 48.0

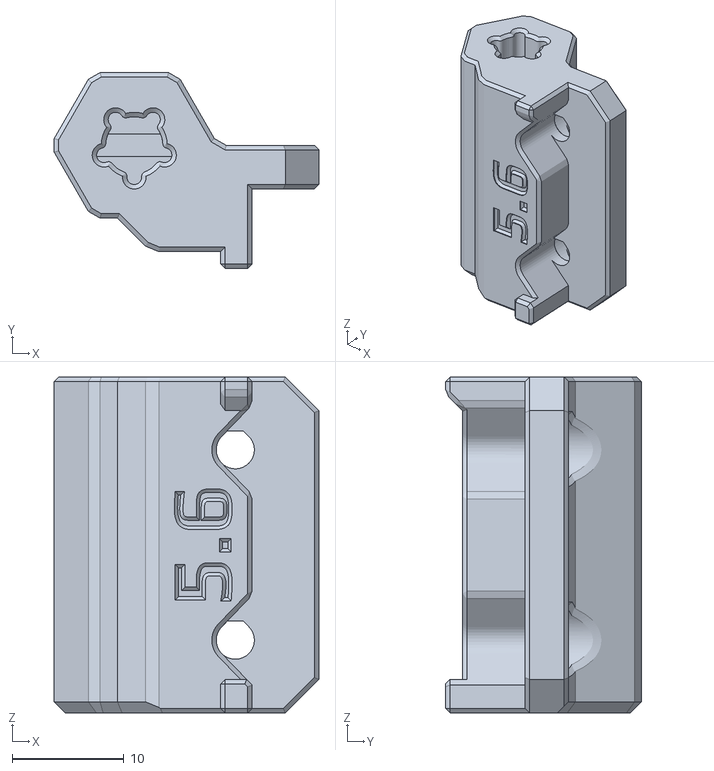
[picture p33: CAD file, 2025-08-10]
STLs/Hinges/Hinge on Left/Bottom_Hinge_Frame_Mount_L/Bottom_Hinge_Frame_Mount_L_5.6mm_x2.stl
23.6 x 17.5 x 30.0

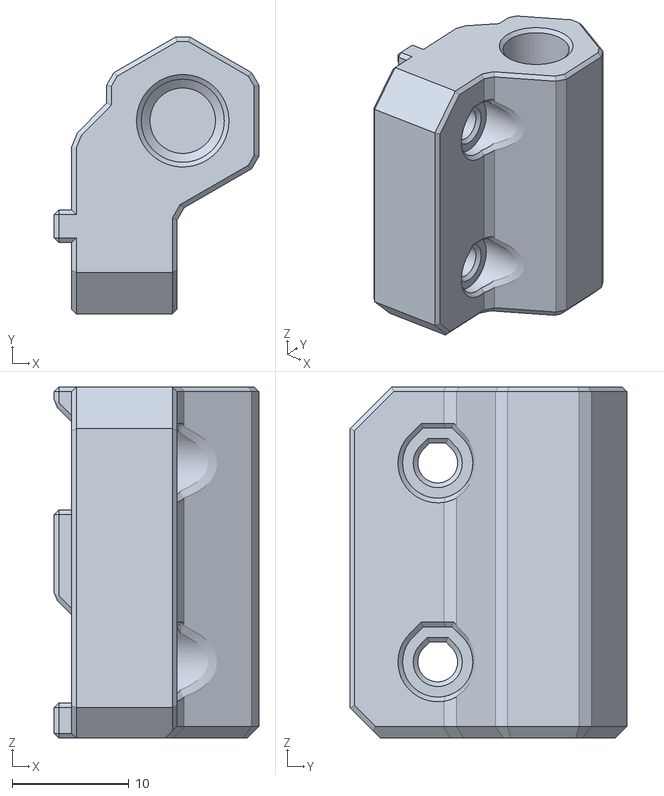
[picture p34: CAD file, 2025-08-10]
STLs/Hinges/Hinge on Left/Top_Hinge_Door_Mount_L_x2.stl
17.5 x 23.7 x 30.0

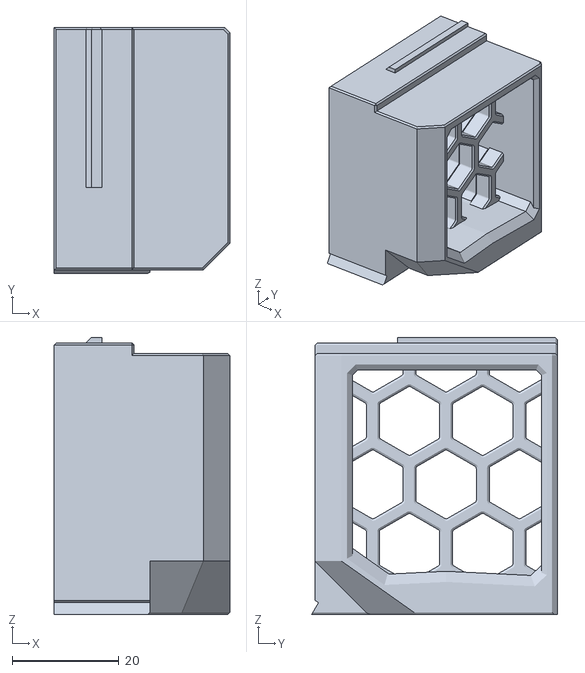
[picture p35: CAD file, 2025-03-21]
STLs/Optional Skirts/Micron+/G2Z v1.1/CC_G2Z_Front_Skirt_B_x1.stl
33.0 x 46.2 x 52.0

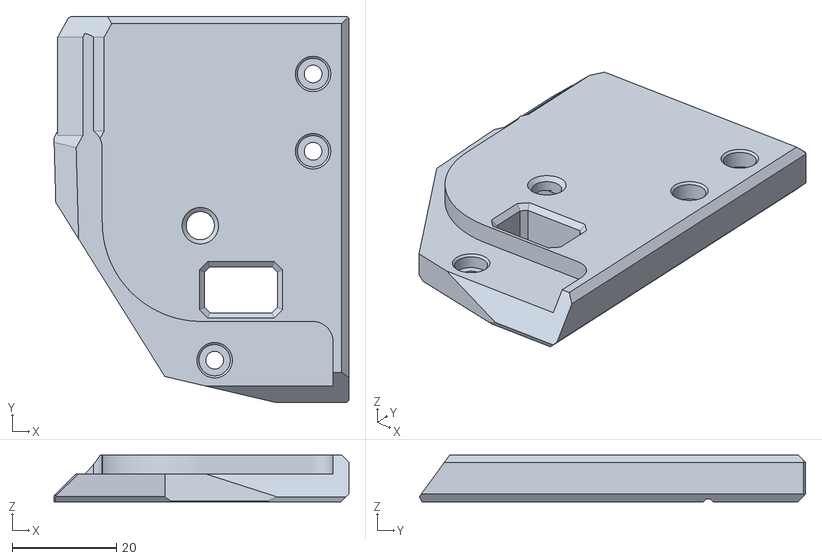
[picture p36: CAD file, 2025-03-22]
STLs/Optional Skirts/Micron+/Stock Z/[a]_CC_Micron_StockZ_Foot_Mount_B_x1.stl
56.6 x 74.2 x 9.00

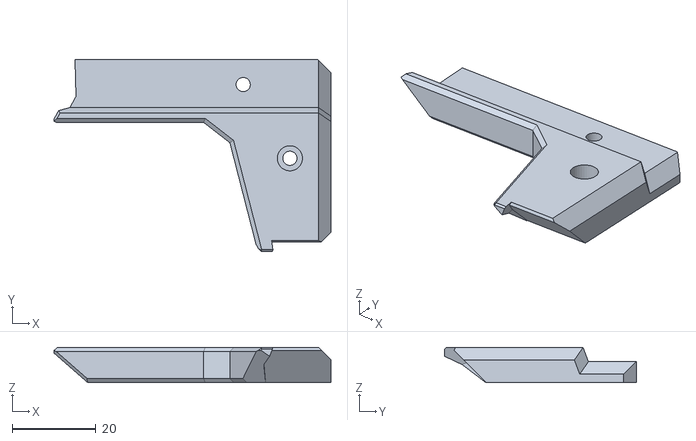
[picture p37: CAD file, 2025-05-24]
STLs/Optional Skirts/Micron+_StealthFork_Common/TFT35/[a]_CC_TFT35_Accent_A_x1.stl
66.1 x 45.8 x 8.40

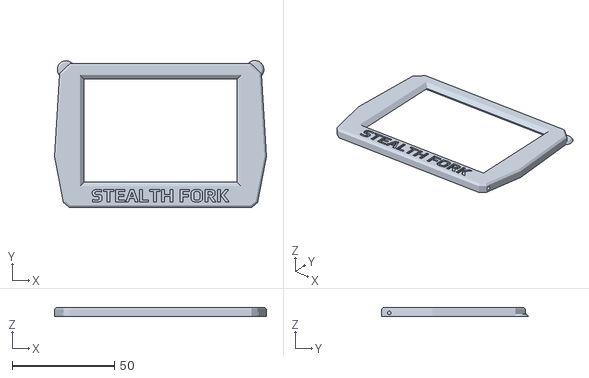
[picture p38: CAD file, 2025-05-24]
STLs/Optional Skirts/Micron+_StealthFork_Common/Waveshare_BTT_43/[a]_CC_TFT35_StF_Bezel_x1.stl.stl
103.9 x 72.0 x 4.60

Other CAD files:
STLs/Optional Skirts/Micron+/Stock Z/CC_Micron_StockZ_Skirt_Main_Body_A_x1.stl
STLs/Handle/Handle_C_Logos/Handle_on_right/Handle_C_Micron_R_x1.stl
STLs/Hinges/Hinge on Right/Bottom_Hinge_Frame_Mount_R/Bottom_Hinge_Frame_Mount_R_5mm_x2.stl
STLs/Hinges/Hinge on Right/Top_Hinge_Door_Mount_R_x2.stl
CAD/Optional Skirts/Archive/CC_MicronPlus_G2Z_Skirts_v1.step
STLs/Handle/Handle_B_x1.stl
STLs/Handle/Handle_C_Logos/Handle_on_left/Handle_C_HX0_L_x1.stl
STLs/Handle/Handle_C_Logos/Handle_on_left/Handle_C_LDO_L_x1.stl
STLs/Handle/Handle_C_Logos/Handle_on_left/Handle_C_MicronHex_L_x1.stl
STLs/Handle/Handle_C_Logos/Handle_on_left/Handle_C_Micron_L_x1.stl
STLs/Handle/Handle_C_Logos/Handle_on_left/Handle_C_PFAHex_L_x1.stl
STLs/Handle/Handle_C_Logos/Handle_on_left/Handle_C_PFA_L_x1.stl
STLs/Handle/Handle_C_Logos/Handle_on_left/Handle_C_SaladForkHex_L_x1.stl
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

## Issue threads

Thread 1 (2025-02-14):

Where are the keys?

EricZimmerman, 2025-02-14:
for the clips similar to annex, where are the keys that go onto the clip? i see it in the cad, but wanted to ask in case it needed added to the stl files.

i did export it and oriented it to be flat

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

Jadecky, 2025-03-11:
Hi Eric, apologies for the delay.

Those are the [Micron R1 twist locks](https://github.com/PrintersForAnts/Micron/blob/main/R1_Beta/STLs/Panels/%5Ba%5D_twist_lock_key_x50.stl)

Good call, I’ll add this to the readme!

Closed 2025-03-12.

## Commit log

2024-10-08 Initial Upload
    Add CAD, STLs, Images, readme
    [Bottom_Frame_Mount_L_x2.stl, Bottom_Frame_Mount_R_x2.stl, CC_G2Z_Front_Skirt_A_x1.stl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]
2024-10-10 Added `Latch_Extra_Clearance` and fixed missing chamfer
    - Added missing chamfer to: `Top_Door_Mount_L_x2`
    - Added missing chamfer to: `Top_Door_Mount_R_x2`
    - Added STL: `[a]_Latch_Extra_Clearance`
    - Corrected naming of `[a]_Latch_Standard`
    - Corrected naming of `Top_Door_Mount_R_x2`
    - Updated CAD to reflect above
    - Updated readme
    [Latch_Standard_x1.stl, Top_Door_Mount_L_x2.stl, Top_Door_Mount_R_x2.stl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]
2024-10-17 Added `Larger Surface Area Latch` & Corrected text on `Latch Hardware Image`
    [[a]_LSA_Latch_Extra_Clearance_x1.stl, [a]_LSA_Latch_Standard_x1.stl]
2025-03-12 fixed [#1](https://github.com/PrintersForAnts/ColonyClacker/issues/1)
2025-03-21 Added Micron+ StockZ Skirts & V1.1 of G2z Skirts
    [CC_G2Z_Front_Skirt_A_x1.stl, CC_G2Z_Front_Skirt_B_x1.stl, CC_G2Z_Skirt_Corner_A_x1.stl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]
2025-03-22 fixed missing heatset hole. Micron Stock Z skirts.
    [CC_Micron_StockZ_Skirt_Main_Body_A_x1.stl, CC_Micron_StockZ_Skirt_Main_Body_B_x1.stl, [a]_CC_Micron_StockZ_Foot_Mount_A_x1.stl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]
2025-05-03 Update readme.md
    Update link to Micron Twist lock key stl
2025-05-17 uploaded cad
    cad for mini monolith and hinges
2025-05-24 Add StealthFork Skirts & TFT35 Display Mount
    [CC_StF160_Corner_A_Skirt_x1.stl, CC_StF160_Corner_B_Skirt_x1.stl, CC_StF180_Corner_A_Skirt_x1.stl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]
2025-08-09 Add User Mod - BTTHDMI5 (#3)
    [(a)_CC_BTTHDMI5_Bezel.stl, (a)_CC_BTTHMDI5_Buttons.stl, CC_BTT_HDMI5_Mount.stl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]
2025-08-09 Add new latch and handle_c logo variants
    [Handle_C_HX0_L_x1.stl, Handle_C_HX0_R_x1.stl, Handle_C_LDO_L_x1.stl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]
2025-08-10 Added panel thickness variations and general clean up
    [Bottom_Frame_Mount_L_x2.stl, Bottom_Frame_Mount_R_x2.stl, Bottom_Hinge_Frame_Mount_L_2.8mm_x2.stl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]
2025-08-10 Updated CAD
